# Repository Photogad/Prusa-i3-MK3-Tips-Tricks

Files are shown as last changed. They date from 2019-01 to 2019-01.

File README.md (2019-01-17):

# Prusa i3 MK3 Tips and Tricks

The following informations are things that I have learned from my 3D printing journey with the Prusa Mk3. I don't claim that everything here is 100% factual, and if you think I am providing any incorrect information, please let me know by posting on my Github Issues list! I am still learning myself, and hope to help others to learn from mistakes I made.

# Table of Contents  

**Getting Up And Running**

• [Spare Parts and Supplies You Should Order Immediately](#spares)

• [Tensioning Belts Properly](#tension)

• [Cleaning Your Bed](#cleaning)

• [Calibrating Live Z My Way](#livez)

• [Calibrating Extruder Idler Tension](#tension)

• [Calibrating Extruder E-Steps](#esteps)

• [Better Slic3r PE Printing Profiles](#profiles)

**Troubleshooting**

• [First Layer Bed Adhesion Issues And How To Fix Them](#flai)

• [PETG Sticking To Bed Too Much](#petgstick)

• [Problems Printing PETG Unless Very Slow Speed Used](#petg)

• [Need More Help?](#help)

**Take Things To The Next Level**

• [Put A Sock On It](#sock)

• [My Optimized Startup GCODE](#gcode)

• [7x7 Mesh Bed Leveling](#7x7)

• [Slic3r PE On Meth](#meth)

• [Using Different Nozzles For Different Results and Speeds](#nozzles)

• [Properly Changing Nozzles](#nozzlechange)

• [Achieving Better Print Quality Through Hardware Upgrades](#quality)

• [Recommended Printable Mods For Your Mk3](#mods)

<a name="spares"/>

# Spare Parts and Supplies You Should Order Immediately

The Prusa MK3 is a machine. Like all machines, it needs regular maintenance. Like all machines, it has parts that break with use and need replacement. Below is a list of parts and supplies I recommend you order right away and always have on hand, if you don't want to have 3D printing down-time.

* [Part Cooling Fan](https://all3dmakers.com/products/mk3-part-cooling-fan). The wires on the part cooling fan are ridiculously fragile. I snapped mine right off just by bumping into them with my hand one time. And unless you are amazing at soldering, you can't fix them nor take the fans apart. Always have one of these in your spare parts bag! I also recommend dousing the wires with superglue where they connect to the fan body, it will help keep them from breaking off as easily in the future.
* [Belts](https://all3dmakers.com/products/gates-ll-2gt-rf-6mm-width-2mm-pitch-for-mk3-mk2-5-belt-for-y-axis). Your belts will eventually break with wear and tear. Or maybe you overtighten them and cause them to break prematurely. Always keep one spare on hand for each axis! And always get genuine Gates LL-2GT belts. THESE ARE DIFFERENT THAN GATES GT2 BELTS. Confusing, I know. But the Gates 2GT belts are made specific to the 2GT idlers that Prusa uses, which are different than the GT2 belts and idlers. (note: link is for Y belt only).
* [Powder Coated Sheet](https://www.amazon.com/Thekkiinngg-Double-Sided-Textured-Powder-Coated-Version/dp/B07HQZCWDV). I highly recommend this aftermarket powder coated sheet, it's so much better than the smooth PEI sheet that ships with the Prusa MK3s (unless you were lucky to get the Prusa Powder Coated Sheet which is better). The PEI on your sheet will eventually wear out and it's a pain in the ass to install new PEI on it (though not impossible) so just better to have a spare metal sheet ready to go, in my opinion.
* [Bearings](https://us.misumi-ec.com/vona2/detail/221000091803/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). Your bearings are eventually going to go, and make your printer axis not glide smoothly and be noisy. The link are for Misumi LM8UP bearings, which are the highest quality bearings you can buy. They are even better than the LM8U Misumi bearings that many recommend to buy (the P stands for precision). You need to make sure to grease them when you get them, they come un-greased! Use [this printed tool](https://www.thingiverse.com/thing:1128781) to grease your bearings with [Super-Lube PTFE](https://www.amazon.com/dp/B0081JE0OO/ref=twister_B07HLTTG9L?_encoding=UTF8&psc=1).
* [Super-Lube with PTFE](https://www.amazon.com/dp/B0081JE0OO/ref=twister_B07HLTTG9L?_encoding=UTF8&psc=1). You are going to need to grease your bearings and Z screws every now and then to keep things running smoothly. I high recommend this type of lube for the Prusa MK3. 
* [16x16x2" Concrete Paver (Stepping Stone)](https://www.homedepot.com/p/Pavestone-16-in-x-16-in-x-1-75-in-Pewter-Square-Concrete-Step-Stone-72600/100346228). This is a thick, heavy slab of rock to put underneath your printer, for several benefits. First of all, your printer is basically an open oven - your hotend will heat up to sometimes 300c depending on what you are printing (that's nearly 600 degrees fahrenheit!). Although most of that heat is just happening in the nozzle and not near your surface, it's much safer to have this very hot thing that melts plastic into lava on a concrete surface that is fire-resistant instead of a wooden desk or workbench, just in case something happens and a fire gets started. But just as importantly, you are giving your printer a much more firm and stable surface with no vibrations, which will improve your print quality immensely and eliminate ghosting and ringing effects in your print quite a bit. Even with my printer on a very heavy duty oak wooden desk before, I saw a noticable difference in print quality. It's best to source one of these very large and heavy concrete pavers from your local hardware store - I got mine for only $2. Buying them online and paying for shipping is much more expensive, which is why I don't recommend buying online. Make sure to get one with a smooth flat surface, and not one with a brick or tile pattern that has grooves and ridges, because you want your printer to be level. Speaking of level - be sure your paver is level! If not, use a shim under any of the corners to level it out. You don't need a bigger one than 16x16x2", but that size is the SMALLEST you will need. So feel free to get a bigger one if you want!
* [Smoke Detector](https://www.amazon.com/Kidde-Battery-Operated-Smoke-Alarm/dp/B00PC5SPPK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). Kind of going off of the last point, this is for safety reasons, but safety alone. 3D printers get very hot, and you should never leave them unattended; but if you need to because of long print times, a smoke detector is a good idea. People's homes have burned down because of 3D printers! The Prusa MK3 is one of the safest printers out there, but it's better to be safe than sorry! Place the smoke detector near your 3D printer, above it on the ceiling if possible. I highly recommend coupling your smoke detector with a [Roost Smart Wi-Fi Battery](http://www.getroost.com/product-battery.html) which will send alerts to your smartphone if your smoke detector goes off!
* [Remote Wi-Fi Power Shut Off](https://www.amazon.com/TanTan-Wireless-Required-Anywhere-Upgraded/dp/B071VYFJRL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). Again for safety, if your printer does happen to catch on fire (knock on wood) and you aren't home, you need a way to shut it off remotely ASAP! You should be monitoring your prints remotely with a web-cam, but wi-fi smoke detector is also useful!

<a name="tension"/>

# Tensioning Belts Properly

It's important your belts are all properly tensioned. Too tight, and you can get backlash (ugly prints), too loose and you can get shifted layer problems (also ugly prints). Now, the Prusa MK3 is kind of unique in that it can tell you what your belt tension is - sort of. To get your belt status numbers, you need to do a self-test (from the Calibration menu), and then after the self-test is done, it will update your belt status numbers which can be seen in the Support menu -> Belt Status. A lower number is a tighter belt, a higher number is a looser belt. Any time you want to get an updated belt status, you need to run self-test again from calibration menu.

Now, the thing about the belt status info is that it doesn't actually measure your belt tension. It instead measures the resistance the X or Y motor encounters when trying to turn, and tries to make a guess at the belt tension. The problem with this is that there can be other factors at play that "fool" the numbers - like belts that are rubbing on the side of the plastic parts or pulleys (not aligned properly), or problems with the motors themselves. 

Even worse is that there's a lot of misinformation out there about what the "perfect" belt status number is. I see 240 being floated around everywhere as the perfect number. That's what I tensioned my belts to. Worked fine for a while, but then one of them snapped on me. OUCH! Good thing I had a spare belt in my drawer.

[Chris Warkocki](https://prusacommunity.com/your-belt-status-and-you/), a pretty big name in the Prusa community that I highly respect, suggests about 270 as being a perfect number for belt status. I totally agree with this, 270 gives me the best results. But just be careful about these numbers. Like I said, the numbers reported on the printer aren't totally accurate. Right now my X belt is reporting 266 and my Y belt is reporting 278, but I can feel for sure that my Y belt is actually tighter. 

So just be very careful about overtightening the belts! You only need your belts tight enough so that the teeth stay engaged in the pulleys without slipping. There is no benefit to having belts tighter than that.

And it's better to have belts on the looser side than the tighter side, in my opinion. Having belts too tight makes it hard for the X and Y axis to move, which must surely put more strain on the motors, as well as decrease the life of the belts.

Ok wait, so how do you actually tension your belts? Well, on the stock MK3 it's kind of hard to do. The X axis has a built-in tensioning screw which is kind of a pain in the ass to really use, and if you tighten it too much it will crack your X axis end printed part (happened to me). So you can use this (follow the Prusa manual) but be very careful. Also, don't expect it to actually tension your X belt too much.  For the Y belt, the only method on stock MK3 to tension it is to loosen the screws that hold the Y belt pulley to the front of the frame, put your belt as tight as possible by hand into the belt grooves on the bottom of the bed, and then tighten the screws in the pulley to pull it tighter. Again, this method really sucks and doesn't allow you to tighten the belt very much.

A much better thing to do is just take the time to upgrade your whole extruder and X axis to the [Bear X axis and Extruder](https://www.thingiverse.com/thing:3226689), and upgrade your Y axis to the [Taurus Y axis](https://www.thingiverse.com/thing:3269389). This will require a lot of printing of parts and a few extra hardware supplies, but it's highly worth it for many reasons, one of them being how easily and convenient they will make it to tension your belts in the future.

<a name="cleaning"/>

# Cleaning Your Bed

In this section, I'm going to tell you how to properly clean the steel sheet on your bed and address a lot of myths.

First of all, yes, cleaning your bed frequently is important. Oils from your hands build up on the bed, and create adhesion issues where the PLA plastic does not want to stick to the bed. It's also very important to clean it before you do your first print because the steel sheet may have some machine oil on it (mine did) from the manufacturing process.

Cleaning is simple - just wet an unscented paper towl with 91% or greater isopropyl alcohol available from most local drug stores, (but I highly recommend [99.9% isopropyl alcohol](https://www.amazon.com/MG-Chemicals-Isopropyl-Alcohol-Cleaner/dp/B0797BZDM5) for the best results) and rub the steel sheet on your bed SIDE TO SIDE (not circular motion) so that you wipe the oils off and not spread them around. Cleaning your steel sheet before your first ever print, and clean it before the first print of any day, should be frequently enough. It only takes 10 seconds to do and is worth it. Side note: 70% isopropyl alohol is actually much better at disinfecting wounds and cuts on your body which is why they sell it. ;)

Occasionally, your steel sheet may become so dirty with oils that isopropyl alcohol just does not cut it. In this case, take the steel sheet off of your print bed, bring it to a sink, and scrub it with unscented dish soap. Then dry it. This is the best method to clean your steel sheet, but is kind of annoying to do!

Keep in mind that if you are printing PETG and not PLA, you actually might want a dirtier sheet! PETG is notorious for sticking well (too well) to the steel sheet, and some people actually wipe nose grease (skin oil) onto the the steel sheet before printing PETG. However, a better solution is wiping the steel sheet with Windex (or any blue window cleaner) before printing PETG. It will help the PETG prints to release from the bed when they are done without damaging the PEI surface on your steel sheet. Just make sure to clean the bed again with isopropyl alchol or unscented dish soap before printing PLA again!

<a name="livez"/>

# Calibrating Live Z My Way

Calibrating your Live Z is the most important thing you can do, because your first layer is the most important layer and is what supports all of your other layers. Unfortunately, the Prusa Mk3's built-in live Z calibration has many flaws. For one, it only works with .40mm nozzle size (stock nozzle). Second, the little square it prints at the end for inspection is very small and prints too fast to make any last minute adjustments. I've found this to be the best way to Calibrate Live Z:

1. Download my [100x100x0.20 calibration STL](https://github.com/photog0411/Prusa-i3-Mk3-Resources/blob/master/Calibration%20STLs/LiveZ100x100.stl) file.
2. Open it into Slic3r and slice it with the following settings:
* 0.20mm Layer Height
* Infill Before Perimeters
* Rectilinear top/bottom infill with fill angle of 90 degrees.
* Bed temp at the bed temp you will use for printing the majority of your things.
3. Now print it! It will begin printing a big live Z calibration square that is much easier to see what's going on than with the built-in Prusa one. Because you did infill before perimeters, it will start much quicker because you don't have to wait for the uneeded permieter to get laid down first. And because you have the infill angle set to 90 degrees, it won't waste filament in the corner of the square where you can't see whta's going on.
4. Press the knob on the front of your printer and enter the live Z adjustment mode.
5. Adjust the live Z number until each line that gets laid down has no gaps between it and the last one. You don't want to smush the plastic down too much where the plastic layer developes ridges in it, but really do not want any gaps. I would actually recommend starting at -0.300 and working your way up from there in -0.100 increments. Once you get to a number that looks good (it was -0.700 for me) you can adjust in smaller increments of -0.025 to get it perfect.
6. If you use multiple nozzle sizes, be sure to make a calibration GCODE for each of your nozzles! I personally have a /calibration/ folder on my SD card and calibrate the live Z whenever I swap nozzles.

<a name="tension"/>

# Calibrating Extruder Idler Tension

It's a good idea to make sure your idler in your extruder has proper tension - too loose and it won't grab the filament well enough, too tight and it will crush the filament and cause extrusion issues. It's very simple to get it tensioned properly!

1. With filament loaded and printer preheated for your filament, undo the two screws (or one screw if you are using bear extruder) that hold the idler door in place. These are the screws with the springs on them.
2. Swing the door open fully, make a black mark somewhere on the filament with a sharpie marker for visual reference.
3. Make your printer move the extruder quite a bit, you can do this from inside the printer menu. At this point, the filament should not be moving even though your extruder motor is moving.
4. Close the idler door lightly, and then start screwing the screws in slowly. You want to keep screwing them in until they JUST start to grab the filament and the filament starts moving and extruding.
5. Once it has just grabbed the filament, tighten the screws just a bit more (a few more complete turns).

Now your extruder idler should be properly tensioned!

<a name="esteps"/>

# Calibrating Extruder E-Steps

It's important that when you tell your printer to extrude 100mm of filament, it actually does extrude 100mm of filament. If it's extruding more than you request, it's over-extruding, and if it's extruding less than you request, it's under-extruding. Overextrusion can make for worse print quality on the ouside edges and cause bridges to sag too much, and under-extrusion can cause your prints to be weaker or not have proper infill. 

This is all controlled in your printer firmware by a thing called E-Steps. By default, the Prusa MK3 E-Steps are set to 280, which should be perfect for most printers. But you should still double check it! Here's how:

1. With filament loaded, move your extruder by hand so that it's directly below the filament spool and the filament is straight up and down.
2. Measure 120mm from where the filament enters your extruder and put a mark 120mm up on the filament with a black sharpie marker.
3. Connect the printer to your computer via USB, open Pronterface, and connect to the printer in Pronterface. 
4. Preheat your printer, wait for extruder to be warmed up, and then use the extrude button and settings in Pronterface to extrude 100mm of filament at 100mm / minute. 
5. Once it's done extruding, measure from the top of the extruder to the black mark you made. It should measure exactly 20mm, because you marked out 120mm but asked the printer to extrude 100mm.

Did you get 20mm left? If so, great! If not, remember the amount you measured and follow the steps below to calibrate:

1. Mark the filament again 120mm from the top of the extruder. 
2. In pronterface, issue M503 command in the terminal. It should return steps value, you want to remember the one that says "EXXX" where XXX is the steps number for extruder. If you have never done this before, it should be 280. Those are your extruder steps value currently.
3. Now subtract the amount that was left over from 120mm in the first instructions. So for example if you had 10mm left over instead of the correct 20mm, you would do 120-10=110. This means that your extruder actually extruded 110mm of filament when you asked it to do 100mm.
4. Multiply your current extruder steps value by 100. So if it was at the default of 280, you would do 280x100=28000.
5. Now divide that big number (28000 in example) by the real amount your extruder did. In above example, we said 110 so you would do 28000/110 = 254.54. This will be your new E-Steps value instead of 280. Now you need to actually change this value and save it in your firmware.
6. In Pronterface terminal, issue command M92 EXXX.XX where the X's are your number. In above example, you would do M92 E254.54.
7. Now issue command M500 to save it to your firmware, and you can also do M503 again to verify that the changes were saved.

Your extruder should now be calibrated and pushing 100mm of filament when you ask for it. But you need to verify that it's correct now!  Just start these steps all over again and mark out the 120mm on the filament, and measure when it's done extruding. You should now have 20mm left when you asked it to extrude 100mm.

<a name="profiles"/>

# Better Slic3r PE Printing Profiles

Here in my repository, I have several printing profiles uploaded into the [/profiles/](https://github.com/photog0411/Prusa-i3-MK3-Tips-Tricks/tree/master/Printing%20Profiles) folder. These profiles are much better than the stock Prusa profiles included with Slic3r PE, especially if you have a well tuned and calibrated printer that is functioning well. 

Here's the list and notes for each profile:

* Pretty PLA V3.5a.ini - This is Chris Warkocki's latest Pretty PLA profile (as of 1/12/2018) for printing with PLA filament. YOU MUST have the [7x7 Mesh Bed Leveling Firmware](#7x7) installed on your MK3 printer to use it as-is, but you can also use it on stock firmware by changing the "G80 N7" command in the start gcode to just "G80". This profile is highly tuned for the best possible results printing with PLA, and you should see a nice difference in print quality! Keep in mind this profile is only made for the standard .40 nozzle size, but you can also duplicate this profile in Slic3r and change nozzle size on the printer tab to whatever size nozzle you are using.
* Pretty PETG V3a(7x7).ini - This is Chris Warkocki's latest Pretty PETG profile (as of 1/12/2018) for printing with PETG filament. YOU MUST have the [7x7 Mesh Bed Leveling Firmware](#7x7) installed on your MK3 printer to use it as-is, but you can also use it on stock firmware by changing the "G80 N7" command in the start gcode to just "G80". This profile is highly tuned for the best possible results printing with PETG, and you should see a nice difference in print quality! Keep in mind this profile is only made for the standard .40 nozzle size, but you can also duplicate this profile in Slic3r and change nozzle size on the printer tab to whatever size nozzle you are using.

To install these, just download the .ini files, open Slic3r PE, go to file menu -> Import Profile. Please note that for any of these profiles, I highly recommend duplicating them and adding [My Optimized Startup GCODE](#gcode) to the profiles instead. ;)

<a name="flai"/>

# First Layer Bed Adhesion Issues And How To Fix Them

**NOTE: The glue stick that ships with the Prusa MK3 does help bed adhesion for PLA, but has the reverse effect when using PETG (makes PETG stick less). But the glue stick is messy and sucks, never use it please. Use the methods below instead.**

Before trying the steps below, make sure you have [calibrated your live Z correctly](#livez). Ignore the Prusa video where Josef says it should be a value of around -1.200. Your value will depend on how far up your PINDA is mounted and how thick your bed plate is. Your live Z value is adjusted properly when the lines of plastic that are laid down do not have any gaps in between them. If you think your live Z is adjusted properly, you may begin the following steps: 

1. Clean your bed plate with [99.9% Isopropyl alcohol](https://www.amazon.com/dp/B005DNQX3C/ref=cm_sw_r_cp_apap_2tu8Mct2ObEU7) and UNSCENTED paper towels. Do not use anything less than 99.9% and do not rub it in a circular motion, rather, rub it from side to side. Your bed plate has oils on it from the manufacturing process, and from whenever you touch it with your oily hands. Your goal is getting the oil off, not spreading it around! It's very important to also use unscented paper towels with no coloring designs as these may have oils in them.  

2. If the isopropyl alcohol fails to help, use unscented dish soap and hot water to clean your bed plate in the sink. Scrub it well, and dry with unscented paper towels. Be sure to not touch the clean bed plate with your hands once washed (grip the edges only). Soap breaks down grease and oils even better than Isopropyl alcohol, but is obviously a more annoying process. If you don't touch your bed plate too much, you should be fine with washing your plate in the sink once per month, and rubbing it with isopropyl alcohol once a day before your first print of the day. 

3. If you are still having issues, try printing your first layer hotter. Hotter plastic is more "liquidy" and will spread on the bed easier, as well as stick better. I personally use 220c for PLA and 265c for PETG first layers. 

4. Make sure fan is disabled for first layer in slic3r. You might even want to disable it for the first 2 or 3 layers for  smaller prints, as your plastic being laid down might be cooling too quickly for it to stick. 

5. Try a warmer bed temperature. I personally find that my bed is actually 5c colder than the printer reports after measuring it with an IR thermometer. So I print with my bed temp at 65c for PLA instead of the default of 60c. 

6. If you are using a smooth PEI sheet, rough it up gently with a scotchbrite pad or fine grit sandpaper. It won't affect your print quality and the rough surface will create more friction for the hot plastic to stick to. 

7. Run the temperature calibration procedure in your printer's options. It will calibrate your PINDA to be more accurate which will help your bed to be more level.

8. Use my startup GCODE below. I've highly optimized it to give the best possible first layer results.

9. If all else fails, buy a powder coated sheet. You can get an aftermarket one on Amazon called [thekkiinngg v3](https://www.amazon.com/Thekkiinngg-Double-Sided-Textured-Powder-Coated-Version/dp/B07HQZCWDV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) for $60. It's a bit pricey, but PLA sticks amazingly well to this sheet,  and I love the textured finish it gives my prints. Once Prusa begins selling their own powder coated sheets again, they will be a better option.

<a name="petg"/>

# Problems Printing PETG Unless Very Slow Speed Used

I had major issues printing PETG using the default Prusa profiles - the infill would just crumble and break. After much trial and error, I discovered the only way to get it to print was to lower the infill speed down ridiculously low to like 15mms. Obviously, this was not preferred. But I was able to eventually get it solved! The easy solution is to just print at 265c for PETG. The Prusa default of 235c is too cold. As someone on the Prusa discord server said to me, "PETG likes it hot". This is absolutely true. After switching to 265c for PETG, it prints faster and more beautiful for me than ever before.

<a name="petgstick"/>

# PETG Sticking To Bed Too Much

PETG is notorious for sticking to the bed too much; and if you are not careful removing the print, you can damage the PEI sticker on your steel sheet. It's kind of the reverse problem of PLA - with PLA you want it to stick more, with PETG you want it to stick less.

But there's four different solutions, and I recommend the third and fourth ones the most.

1. Wipe some nose grease off of your face and rub it onto the bed. The oils from your face will make the PETG stick less. However, if you can do this easily, you are probably a nasty person that never showers or washes their face, so please shower and scrub more often. I'm only joking of course, but seriously there are better, more reliable methods below.
2. Wipe the steel sheet with a glue stick (Prusa includes this with the printer). The glue stick helps PLA stick to bed more, but for PETG is has the reverse effect and actually makes PETG stick less. However, glue stick is messy and I really don't recommend it at all.
3. Wipe the steel sheet with Windex (or any blue window cleaner). Although it doesn't keep the PETG from sticking quite as well as the glue stick, it's much easier to use and a lot less messy! And it works well enough for 99.9% of PETG prints (unless you are printing something very big with a lot of surface area on the bed).
4. Buy a [powder coated sheet](https://www.amazon.com/Thekkiinngg-Double-Sided-Textured-Powder-Coated-Version/dp/B07HQZCWDV). These sheets are much better than the smooth spring steel sheets. With a powder coated sheet, your PLA will stick more and your PETG will stick less. AWESOME!

<a name="sock"/>

# Put A Sock On It

I really recommend buying a pack of [silicone socks for the E3D hot end](https://e3d-online.com/v6-silicone-socks-pack-of-3). They are cheap, easy to install, and have several advantages! First of all, they help insulate your hot-end so it stays at a more stable temperature. Second, they make it so that melted plastic won't stick to your hot-end, so you won't have the "Blob of death" issue where you leave a print unattended for hours and come back to find a big blob of plastic stuck to your hot-end that is near impossible to remove. Although my temperatures are much more stable with one installed, I didn't really see an improvement in print quality, but a more stable temperature is never a bad thing.

<a name="gcode"/>

# My Optimized Startup GCODE

The following startup GCODE is my custom version which has several advantages over the default Prusa startup gcode. First, it waits until the PINDA is at or below 35c before it does anything, and it enables the print fan to help cool it down quicker in case it's already too warm. It then proceeds to preheat the nozzle to warm temperature (but not the actual print temperature) so that when the printer is doing the automated bed leveling, you do not get plastic leaking everywhere. It sets a standardized bed temp of 65c for the automated bed leveling procedure (change this to whatever bed temperature you do your live Z adjust at) because studies have shown that doing the mesh bed leveling at the same temperature that you did your live Z adjust will be the most accurate. Then, it warms up and waits for your PINDA to reach 35c because studies have also shown that the PINDA is the most accurate after it has warmed up to 35c or warmer and does the mesh bed leveling. Finally, it warms everything up to your real printing temperatures, turns the print fan on so you don't get any ooze, runs an advanced purge line that purges better and is easier to remove from your bed (PETG!), and finally your print begins. 

**NOTE: AS OF 1/12/2018, MY GCODE BELOW WILL ONLY WORK ON THE PRUSA MK3 WITH THE CUSTOM [7X7 MESH BED LEVELING FIRMWARE](#7x7) INSTALLED. YOU CAN STILL USE IT ON MK2 AND MK3 WITH STOCK FIRMWARE BY CHANGING THE "G80 N7" line to just "G80"**

```M83  ; extruder relative mode

; PINDA cooling
M104 S0 ; Turn off nozzle heat if it's on
M140 S0 ; Turn off bed heat if it's on
M106 S255 ; turn on fan to cool PINDA
M860 S35 ; wait until PINDA is <= 35C
M106 S0 ; Turn cooling fan off if PINDA is cooled

; PINDA warming and Nozzle Preheating
M104 S170 ; preheat nozzle temp for no-ooze and heat up PINDA in the process
M140 S70 ; heat up PINDA quicker by heating bed to hotter temperature
G28 W ; go home without mesh bed leveling

; Mesh bed leveling with standardized bed temp and warm PINDA
M860 S35 ; wait until PINDA is >= 35C
M140 S65 ; set standardized bed temp for mesh leveling
M190 R65 ; wait for bed temp to finish
G80 N7 ; 7x7 mesh bed leveling @ 65c bed temp across all filament types. Do your first layer calibration at this temp!

; Goto start corner and come up to final temp
G1 Y-3.0 F1000.0 ; go outside print area
M106 S255 ; Turn cooling fan on to prevent oozing and make purge line easier to remove
M104 S[first_layer_temperature] ; set extruder temp for printing
M140 S[first_layer_bed_temperature] ; set bed temp for printing
M109 R[first_layer_temperature] ; wait for extruder temp
M190 R[first_layer_bed_temperature] ; wait for bed temp to finish

; Start the improved purge line
G92 E0.0 ; reset extrusion distance
G1 E2 F1000 ; de-retract and push ooze
M106 S0 ; Turn cooling fan off now for enough time to stop spinning
G1 X20.0 E6  F1000.0 ; fat 20mm intro line @ 0.30
G1 X60.0 E3.2  F1000.0 ; thin +40mm intro line @ 0.08
G1 X100.0 E6  F1000.0 ; fat +40mm intro line @ 0.15
G1 E-0.8 F2100; retract to avoid stringing
G1 X99.0 E0 F1000.0 ; -1mm intro line @ 0.00
G1 X110.0 E0 F1000.0 ; +10mm intro line @ 0.00
G1 E0.6 F1500; de-retract
G92 E0.0

; And a beep to let us know the print is starting!
M300 S100 P10 ; chirp - optional
```
Note: Improved purge line taken from [Bob's Project Notebook](http://projects.ttlexceeded.com/)'s custom gcode.

<a name="7x7"/>

# 7x7 Mesh Bed Leveling

On the stock MK3, it does a 9-point mesh bed leveling before each print. With custom firmware, it's possible to do a 7x7 mesh leveling (49-point) procedure using custom start GCODE. The advantage of doing this is that it will lead to a much more level and accurate bed while printing, if your bed was not very level to begin with or if your steel build sheet has imperfections. The disadvantage to using this is that it will add about a minute to the start of your print, because it's takes longer for the nozzle to move to 49 points and measure them instead of only 9. Personally, I prefer waiting the extra minute to ensure I have a perfectly level bed!

You can [download it here](https://github.com/prusa3d/Prusa-Firmware/files/2715148/Prusa-Firmware-3.5.1-7x7.zip). Please note that the link is for the most recent version as of writing this (1/12/2019), v3.5.1 of the firmware. When Prusa releases the next version of their official firmware, you will have to wait for the firmware modder to add a new version, or temporarily flash to the official Prusa firmware and stop using the 7x7 mesh bed leveling for a period of time. If you join the Prusa Community facebook group, you can [check in the files section for updated releases](https://www.facebook.com/groups/prusacommunity/files/).

To flash to this firmware, simply download the .hex firmware file, connect your MK3 to your computer via USB, and flash the firmware file onto the printer using Slic3r PE.

To actually use the 7x7 mesh bed leveling, you have to insert the G80 N7 gcode command somewhere before your print starts, using the custom start gcode window in Slic3r PE. Or, you can use [My Optimized Startup GCODE Script](#gcode) which already has the 7x7 built into it.

<a name="meth"/>

# Slic3r PE On Meth

A wonderful github user named [Supermerill](https://github.com/supermerill) has created a custom version of Slic3r PE called [Slic3r++](https://github.com/supermerill/Slic3r). I highly recommend using this version, because it has a lot of new features that the official Slic3r PE is lacking, such as but not limited to top surface ironing, XY hole compensation, continuous perimeter loops, interior top layer supports, avoiding unsupported perimeters, and more! Supermerill  keeps his version current with the latest release of Slic3r PE (so you won't miss out on anything from the main version!) and he's really smart (he's actually the guy that invented Gyroid infill). 

<a name="nozzles"/>

# Using Different Nozzles For Different Results And Speeds

One of the best things you can do with 3D printing is using different sized nozzles. The stock Prusa MK3 comes with only a 0.40mm nozzle, but you can get nozzles in a range from 0.15mm to 1.00mm. Using a bigger nozzle will allow you to print things faster and create stronger functional parts, but printing with a smaller nozzle will allow you to print finer details and make nicer looking prints at the expense of speed. I personally recommend buying 0.15, 0.25, 0.60, and 0.80 only (in addition to your 0.40) for a total of 5 different nozzles. I also recommend buying only genuine E3D nozzles (is it worth it to buy a cheap knock-off brand to save only a dollar or two?) and I recommend buying only [hardened steel](https://e3d-online.com/hardened-steel-nozzles-v6) (or better yet, [Nozzle X](https://e3d-online.com/blog/?p=1006)) nozzles so that you can print with abrasive filament such as wood-fill or carbon fiber (these materials will damage regular brass nozzles).

With a smaller nozzle, you are able to print much more small or detailed objects. They are really great for making tiny miniature figurines with very great detail! But the 0.25mm and 0.15mm nozzles print things very slow - a 3 hour print on the 0.40mm nozzle could take as long as 15 hours with the 0.15mm nozzle! So I really recommend using these smaller nozzles only for very small prints, or prints that you absolutely need the best detail for.

With a larger nozzle, you can print quicker (because your nozzle is laying down wider lines of plastic); and because the lines are thicker, your functional parts will be stronger.

Using a 0.80mm nozzle, you can print almost twice as quick as the standard 0.40mm nozzle - your 16 hour print can now take only 8 hours! That's a great time savings. But why don't I recommend the 1.00mm nozzle? Because the stock E3D v6 hotend can only melt plastic so fast and push it through the nozzle so fast, and in order to use the 1.00mm nozzle you have to drastically lower your print speeds in Slic3r, which negates the time savings of using a larger nozzle. The only reason at all I would recommend using the 1.00mm nozzle is to make the strongest parts possible. If you upgrade your hot-end to an E3D volcano hot-end, you can use the 1.00mm nozzle efficiently (and even print with the other nozzles at faster speeds), but it requires a lot of tinkering and modding of your printer that I don't want to write about. ;)

<a name="nozzlechange"/>

**So how do you change nozzles the proper way once you have them?**

Changing your nozzles seems very complicated, but with practice and the right tools, you can do it in 2 minutes flat like I do. I'm so good at it now that I usually change nozzles before each print depending on what I'm printing! Before starting, I recommend getting and making the following tools:

* [16mm Spanner Wrench](https://www.amazon.com/TEKTON-16-Combination-Wrench-18286/dp/B00Q01OBS0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). You will use this to hold your heat block in place. You can also use needle nose pliers but the wrench is much better.
* [E3D Nozzle Change Tool](https://www.thingiverse.com/thing:3277211). You can print and make this tool - I highly recommend it! Or you can just use the standard [7mm E3D spanner](https://e3d-online.com/e3d-7mm-nozzle-spanner) instead, but it's a bit slower to use. If using the standard E3D spanner, please wear leather gloves while doing the nozzle change procedure for safety.
* [E3D Nozzle Holder](https://www.thingiverse.com/thing:3280665). Optional, but a nozzle holder you can print to safely store all of your nozzles.

Once you have those items, you can change your nozzle! Just do the following steps:

1. Preheat your printer for the filament currently loaded, and once it's preheated, unload the filament. Skip this step obviously if no filament is loaded.
2. Move your extruder so that the X-axis is almost to the top of your printer, so you can see and work with the nozzle the best. You can do this by holding in the knob on the front LCD panel on the printer and turning the dial.
3. Now carefully remove your front print fan by releasing it's screws, and tuck your print fan between the X axis belts. Be very careful, the wires on the print fan are fragile and can break if you are not careful.
4. Remove the fan duct that the front print fan was sitting in by releasing it's screw.
5. Now heat your nozzle up to 280c and wait for it to come up to temp. This is an important step because you never want to screw and unscrew the nozzles while the heat block is cold, and you want to do it when the heatblock is past it's thermal expansion temperature, which is about 270-275c for the stock aluminum heat block.
6. Place a soft cloth or rag on your print bed.
7. **This thing is EXTREMELY HOT, SO BE CAREFUL**. Take your 16mm spanner wrench (or needle nose pliers) and put a firm grip on the front of the heatblock so it cannot twist while you are unscrewing your nozzle. Be very careful where you place the wrench on the heatblock so you are not close to the wires (the wires are very fragile). The goal is to stop the heatblock from twisting and breaking the heat break tube inside. You don't need to put a super hard crocodile grip on this thing, just enough grip so it's steady when unscrewing the nozzles.
8. Using your E3D Nozzle Change Tool or 7mm spanner, put it on the hex part (6-sided flats) at the top of the nozzle and unscrew it by turning it counter-clockwise. You will have to unscrew it quite a bit before it comes out all the way. It might fall and hit your print bed, which is why I recommend putting the cloth or rag down to protect it. If you are using the 7mm spanner, this will definitely happen, so also be careful of your fingers and hands because the nozzle will burn you severly if it touches your hand when it falls. This is why I highly recommend using the E3D Nozzle Change Tool because it will support the nozzle on the bottom and prevent it from falling. Even better is to wear a nice set of gloves while doing this.
9. Make sure you are gripping the heatblock with the 16mm wrench again so it does not turn or twist.
10. Now screw the new nozzle in, clockwise. You want it to be snug, but don't overtighten it or you can break the heatbreak inside the hot end.
11. Finally, re-install your fan duct and front print fan in the reverse order you took them apart, and cool down your printer. I also recommend only keeping one of the fan screws installed so it's quicker to remove the fan in the future when you are changing nozzles - one screw is more than sufficient to keeping your fan in place and sturdy.

You have now successfully installed a new nozzle.  Be sure when slicing new prints, you are using correct nozzle side settings! Slic3r PE comes with built-in profiles for 0.25, 0.40, and 0.60 nozzles, but if you are using another sized nozzle you can easily duplicate these profiles and set a new nozzle side under the "printer" tab in Slic3r PE.

<a name="quality"/>

# Achieving Better Print Quality Through Hardware Upgrades

There are many things you can do to your Prusa MK3 printer to make it print objects at higher quality. Mostly, it will be print settings in Slic3r that you will have to tweak with trial and error on a per object basis. But let's discuss acheiving better quality with better hardware!

The Prusa printers are known to be cursed with a problem called the [602 Inconsistent Extrusion Issue](https://github.com/prusa3d/Prusa-Firmware/issues/602). Follow that link for example photos and more information. Basically, it leads to layer lines on the sides of your prints sticking out our being recessed in at spots which is very noticable. This is very hard to correct 100%, but there are some things you can do to help fix this problem a bit - those are listed below. The main cause of this issue is inadequate heatbreak cooling.

There are also other hardware upgrades listed below that not only correct the 602 issue, but also improve print quality in other ways. I ordered them from what I believe to have the biggest affect on print quality to least. Also check out the "printable mods" section following this section for more things that will help increase your quality!

* [Sunon Extruder Fan](https://www.digikey.com/product-detail/en/sunon-fans/MF40100V1-1000U-G99/259-1836-ND/7927772). The stock Noctua fan that ships with the MK3 is weak - something like only 20% as powerful as the fan E3D recommends. This Sunon fan is a replacement fan for the default Noctua fan that ships with the printer. It is much more powerful, at the expense of being louder. But it will help your 602 extrusion issues very much by cooling your heatbreak much better! I highly recommend this fan to replace the stock fan. Make sure you get the MF40100V1-1000U-G99 model, no matter where you order it from. The "V1" denotes the fan speed as "high speed". The V2 is a slower "medium speed" fan and you don't want it.
* [Bondtech BMG Extruder](https://www.bondtech.se/en/product/prusa-i3-mk2-5-mk3-extruder-upgrade/). This is a whole new extruder  for your Mk3, and it's expensive. But because it has much better cooling than the stock extruder and a better gearing ratio, it has been shown to almost completely eliminate the 602 Issue and allows printing at higher resolution.
* [Misumi LM8UP Bearings](https://us.misumi-ec.com/vona2/detail/221000091803/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). These are arguably the best bearings available for your printer. They might increase print quality slightly, as well as make your printer slightly quieter. They will also last longer than the stock bearings that ship with the MK3. You need to make sure to grease them when you get them, they come un-greased! Use [this printed tool](https://www.thingiverse.com/thing:1128781) to grease your bearings with [Super-Lube PTFE](https://www.amazon.com/dp/B0081JE0OO/ref=twister_B07HLTTG9L?_encoding=UTF8&psc=1). You should also get matching Misumi rods (below)! You will need 3 bearings for the X axis, 3 bearings for the Y axis, and 4 bearings for the Z axis. However, X and Y axis are most important if you want to save some money, the Z axis is not as important.
* [Misumi Rods](https://us.misumi-ec.com/vona2/detail/110302634310/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). These rods are more precise than the stock rods that ship with the Prusa MK3. They are matched to the Misumi bearings above. You will need a total of 6, 2 of each of the following lengths: 320mm, 330mm, 370mm.
* [Better Thermal Paste for your Heatbreak](https://www.amazon.com/Thermal-Grizzly-Kryonaut-Grease-Paste/dp/B011F7W3LU). Since we know that one of the leading causes of the 602 Issue is bad heatbreak cooling, it couldn't hurt to put a higher quality thermal paste on your heatbreak. Simply unscrew the heatsink from the heatbreak, remove the old thermal paste, and apply the new paste gingerly to the threads. This probably won't help a whole lot, but it can't hurt! The link above is for Thermal Grizzly Kryonaut paste which is very good and what I'm using, but if you want the very best paste look into something called CooLaboratory Liquid Pro - it's the very best paste you can buy, but very expensive.

<a name="mods"/>

# Recommended Printable Mods For Your Mk3

Below are mods I highly recommend you make for your MK3. They will either make your life easier, or improve the quality of your prints. Maybe both.

* [Bear Extruder and X Axis](https://www.thingiverse.com/thing:3226689). This is a whole new extruder and X-axis for your Mk3, but everything is printable. It's a big project, but very much worth it. It will increase your print quality, make it easy to tension your X axis belt, and also make your printer easier to take apart or fix in the future. I highly recommend it, but make sure to print a [compatible fan duct](https://www.thingiverse.com/thing:3320490) for it too!
* ~~[Taurus Y Axis](https://www.thingiverse.com/thing:3269389). This is a new Y motor mount and belt system, mostly all printable as well. It is much stronger than the default Y axis parts, and allows you to easily tension your Y axis belt. You may notice a slight increase in print quality with this.~~ AS OF 1/17/2018 JLTX IS NO LONGER OFFERING THE TAURUS Y AXIS FOR DOWNLOAD. CHECK THE MOTOR MOUNT BELOW FOR A BETTER Y MOTOR MOUNT.
* [Juiced Y-Motor Mount](https://www.thingiverse.com/thing:2777432). This is a sturdier Y-motor mount for your MK3 that is more durable and might keep your Y motor and belts aligned better.
* [Rigid Feet for MK3](https://www.thingiverse.com/thing:3082188). The rubber feet with the Prusa MK3 are great for making the printer slightly quieter, but upgrading to rigid feet (printable) will improve quality and help eliminate ringing and ghosting effects!
* [Bed Bearing Holder Clamps](https://www.thingiverse.com/thing:2984280). Do you remember how much of a pain in the ass it was to install the bearings to the bottom of your bed using those stupid U-bolt things? Well, print 3 of these puppies out and it will make your life a lot easier in the future if you ever have to change out the bearings. They also made my bed a little bit quieter! Just be careful before installing these, they will NOT work on a stock MK3 frame with M3 Nuts in them (they will bump into the frame), you have to get heat-press inserts (threads!) instead to put in these! Just search online for Brass M3 Heat-Press Threaded Inserts, you will want ones 3mm in length. They are fairly cheap.
* [Improved Z Motor Mounts](https://www.thingiverse.com/thing:2775169). These improved Z-motor mounts will fix some leveling issues with the stock Z motor mounts, make them sturdier, and also make it easier to take your printer apart in the future because they are modular and have a slot! I highly recommend installing these.
* [Mk3 Dust Filter](https://www.thingiverse.com/thing:2983334). Easily print and make a dust filter for your extruder. This will help prevent nozzle clogs from happening by filtering dust from your filament. This is only compatible with stock extruder, not bear extruder.
* [Extruder Visualizer](https://www.thingiverse.com/thing:2638857). Decorate your extruder, but at the same time be able to see what your motor is doing. Great for troubleshooting extruder movements. There are many other design available on thingiverse, or you make your own. All you need is a magnet and some glue.
* [E3D Nozzle Holder](https://www.thingiverse.com/thing:3280665). A great way to store your E3D nozzles if you have a bunch of them.
* [E3D Nozzle Change Tool](https://www.thingiverse.com/thing:3277211). Change your nozzles very easily if you have multiple nozzles.
* [Prusa Mk3 Top Tool Holder](https://www.thingiverse.com/thing:3175038). Conveniently store and access the most frequently used tools.

<a name="help"/>

# Need More Help?

Read Bob's Project Notebook:

http://projects.ttlexceeded.com/

Check out the Prusa Owner's Wiki:

https://github.com/mcm001/prusaOwnersWiki

Post on Reddit:

https://www.reddit.com/r/prusa3d/

Or ask a question in the 602 Wasteland Discord Chat for more immediate help:

https://discord.gg/hYUjSnW

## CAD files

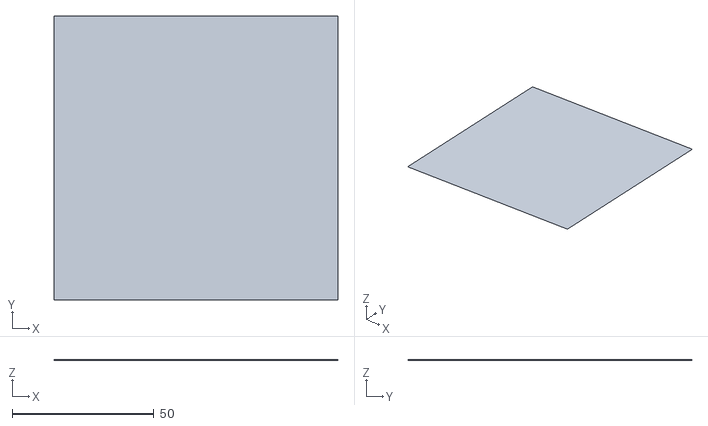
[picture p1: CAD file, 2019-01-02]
Calibration STLs/LiveZ100x100.stl
100.0 x 100.0 x 0.2

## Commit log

2019-01-10 belt tension, spare parts, rigid feet
2019-01-10 more belt tension info
2019-01-10 more info about bearings
2019-01-10 add info about bed bearing clamps
2019-01-12 add z motor mounts
2019-01-12 add nozzle info
2019-01-12 add petg info and bed cleaning
2019-01-17 new sunon fan info and Y motor mount info changed
    new sunon fan info and Y motor mount info changed
